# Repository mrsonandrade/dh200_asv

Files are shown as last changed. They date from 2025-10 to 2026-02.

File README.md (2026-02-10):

## DH200 ASV (Dragon Head 200 Autonomous Surface Vessel)

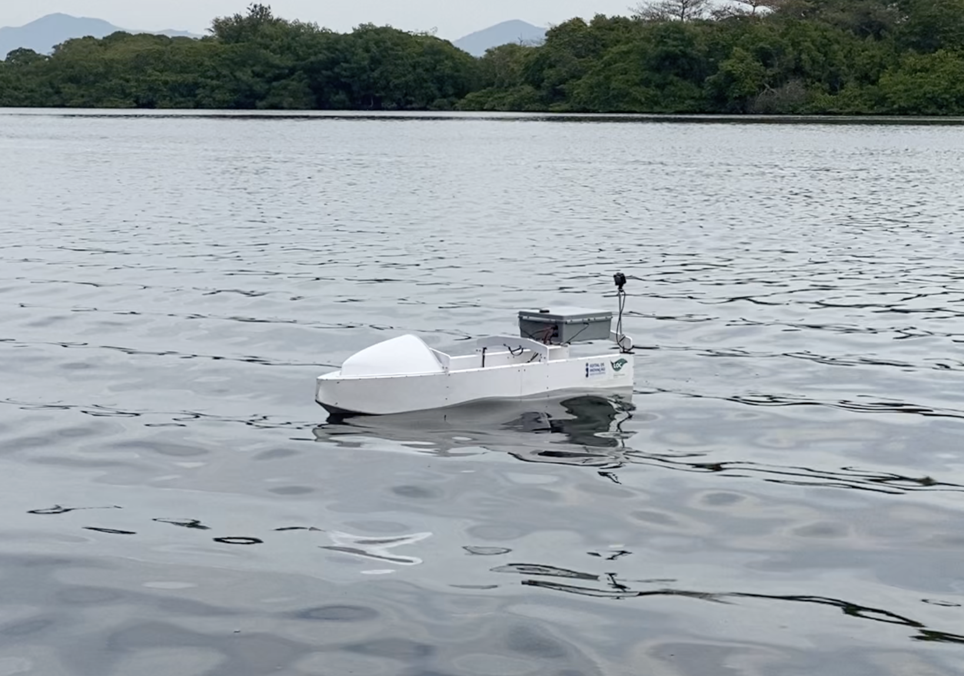
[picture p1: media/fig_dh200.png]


### .

Watch the video (https://www.youtube.com/watch?v=OJGZz4xJ2k4)

## Description

`dh200_asv` is a repository for the paper "A low cost, open-source, multipurpose autonomous surface vehicle".

The repository is structured by folders, each one with the following content:

- **`loc_mind`** – the “operating system” that runs inside the Raspberry Pi is here, as well as the graphical user interface (GUI) that runs in the land station. All the code is written in Python. Here, we call **LOC MIND** the _Modular Intelligent Navigation Device (MIND)_ created at the _Laboratório de Ondas e Correntes (LOC)_.
- **`rhino_files`** – a 3D CAD model for those who are familiar with the Rhinoceros software. This model contains the fully-opened hull configuration.
- **`fusion_files`** – a 3D CAD model for those who are familiar with the Fusion software. This model contains the fully-opened hull configuration with all details of screws, PVC sheets, electronic box, and so on.
- **`cnc_files`** – CNC (Computer Numerical Control) router files for those interested in replicating the hull of the ASV. The files (CRV3D format) are already prepared to be used in CNC machines.
- **`hydrostatics`** – this folder contains the hydrostatics table and the stability table, which are crucial for those planning to explore the capabilities of the ASV.
- **`hydrodynamics`** – as illustrated at the beginning of the paper, this folder contains tables of added mass and damping, load RAOs (Response Amplitude Operators), and displacement RAOs.
- **`docs`** – the main steps to replicate the ASV hull and electronics are in this folder, which contains PDF files and spreadsheets.
- **`media`** – this folder contains pictures and videos of the built ASV.

## Citing the Project

If you make use of the DH200 for your research, please cite our publication. Here is the corresponding BibTeX entry:

```
@article{Benatti2025,
  title = {A Low-Cost,  Open-Source,  Multi-Purpose Autonomous Surface Vehicle},
  volume = {13},
  ISSN = {2077-1312},
  url = {http://dx.doi.org/10.3390/jmse13122380},
  DOI = {10.3390/jmse13122380},
  number = {12},
  journal = {Journal of Marine Science and Engineering},
  publisher = {MDPI AG},
  author = {Benatti,  Thomaz Augusto Kras and de Andrade,  Emerson Martins and Correa,  Maicon Rodrigo and Lopes,  Felipe da Silva and Bernardino,  João Paulo Machado dos Santos and Sales,  Joel Sena and Fernandes,  Antonio Carlos},
  year = {2025},
  month = dec,
  pages = {2380}
}
```

## Contributing to the project
All kind of contributions are welcome: 
* Improvement of code with new features, bug fixes, and  bug reports
* Improvement of documentation
* Additional tests

If you have any ideas or questions, feel free to open an issue or contact us.

## Acknowledgements
The authors would like to thank the Programa de Recursos Humanos da Agência Nacional do Petróleo, Gás Natural e Biocombustíveis (PRH18-ANP) for their support, supported with resources from investment by oil companies qualified in the P, D\&I Clause of ANP Resolution no. 50/2015. This work was supported by the National Council for Scientific and Technological Development (CNPq), the Foundation for Research Support of the State of Rio de Janeiro (FAPERJ) through the ''Jovem Cientista do Nosso Estado'', the Instituto Reditus through the ''Edital de Inovação'', and [LOC/COPPE/UFRJ](https://www.loc.ufrj.br/index.php/en/) ([Laboratory of Waves and Current](https://www.loc.ufrj.br/index.php/en/) - [Federal University of Rio de Janeiro](https://ufrj.br/en/)).

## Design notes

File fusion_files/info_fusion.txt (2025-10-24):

Mass (only the electronics box):	3500 g
Dimensions electronics box (X,Y,Z): 375, 310, 140 mm
Centroide electronics box (X,Y,Z) : 255, 0, 405 mm
Mass (hull + electronics box):	32820 g

DATA (hull + electronics box):
Center of mass (same ref. as in Rhino):	756, -1, 156 mm
Moment of inertia w.r.t. the center of mass   (g mm^2):
	Ixx	1.459E+09
	Ixy	6.057E+06
	Ixz	1.792E+08
	Iyx	6.057E+06
	Iyy	1.060E+10
	Iyz	-2.794E+05
	Izx	1.792E+08
	Izy	-2.794E+05
	Izz	1.102E+10

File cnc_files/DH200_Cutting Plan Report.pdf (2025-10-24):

Cutting Plan Description

Issued by: Felipe da Silva Lopes Approved by: Joel Sena Sales Jr & Antonio Carlos Fernandes
ASV01 - CPR.A | Issued: 10/22/2025
PROJECT | Code: | ASV01
| Title: | DH-200 ASV – Cutting Plan Report
| Client: | Laboratory of Waves and Currents
| Effective date: | October 2025
| Manager: | Emerson Andrade
| Coordination: | Joel Sena Sales Jr & Antonio Carlos Fernandes

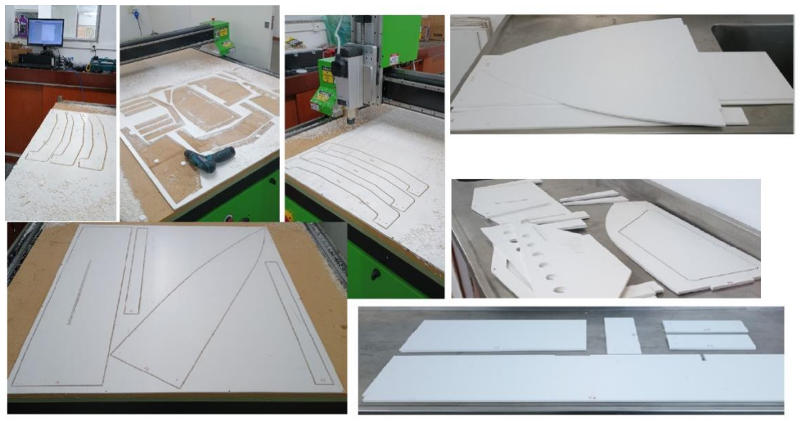
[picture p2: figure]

REPORT | Code: | CPR
| Title: | DH-200 – Cutting Plan Report
| Author: | Felipe da Silva Lopes
| Type: | Cutting Plan Description
| Revision: | A
| Issued: | 10/22/2025

Universidade Federal do Rio de Janeiro COPPE – Instituto Alberto Luiz Coimbra de Pós-Graduação e Pesquisa de Engenharia Laboratório de Ondas e Correntes (LOC)

ASV01 - CPR.A | 10/22/2025 | Page 2 of 10

### DOCUMENT HISTORY

Revision | Date | Issued by | Reviewed by | Approved by | Comments
A | 10/22/2025 | FSL | EA | EA | First version.
Revision | Date | Issued by

Reviewed
by

Approved
by | Comments

Notes:

FSL = Felipe da Silva Lopes

EA = Emerson Andrade

Laboratório de Ondas e Correntes (LOC)

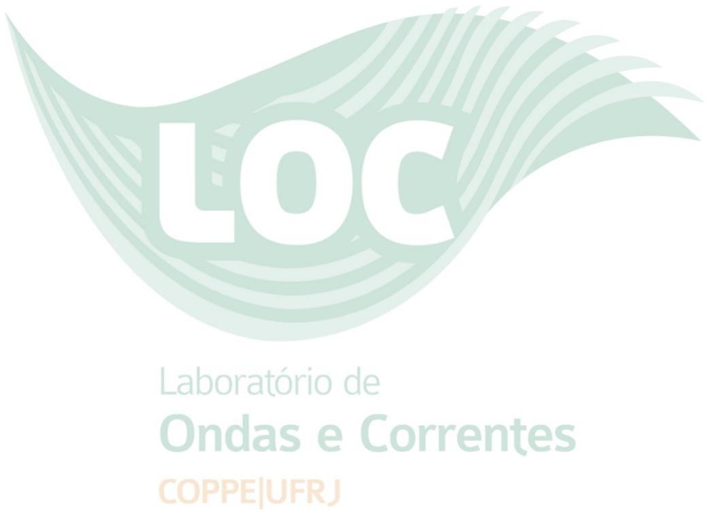
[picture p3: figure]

This document corresponds to an internal report referring to a procedure performed at the

Laboratory of Waves and Currents (LOC – COPPE/UFRJ) and all rights are reserved thereto. Any

partial of full reproduction of the contents in this report without proper authorization is

prohibited, under penalty of adopting appropriate measures in the civil and criminal spheres if

necessary.

Laboratório de Ondas e Correntes (LOC)

### TABLE OF CONTENTS

Laboratório de Ondas e Correntes (LOC)

### 1. Introduction

This document aims to provide step-by-step guidance on cutting parts for the Autonomous Surface Vessel (ASV) hull. The cutting process began with the receipt of the 3D file in Rhinoceros format (.3dm) with the parts properly identified. The parts were then flattened, their respective cut lines, holes, roughing, and other details to be machined were extracted, and the files were saved in .dxf format. Aspire-Vectric CAD/CAM software was used to program the machining tools for each cutting stage and plan the cutting sequence according to the assembly sequence. The CNC router was activated and configured for the origin (zero points), to receive the files saved in Mach 2/3 Arcs (mm) (*.txt) format, and loaded into the Mach 3 CNC software, where the commands and cutting coordinates for the parts were executed (see Figure 1).

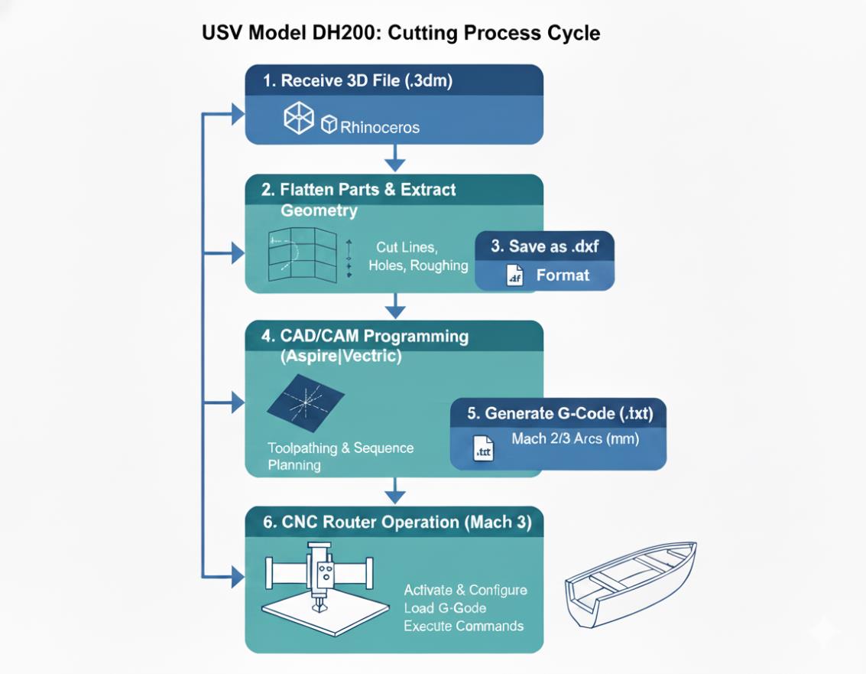
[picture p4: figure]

Figure 1 - Cutting Process Cycle.

Laboratório de Ondas e Correntes (LOC)

### 2. Plate development

In this process, Rhinoceros software was used to create a separated file for manipulating the hull plates. These parts were separated by thickness so they could be pre-arranged. The development was done using the unrollsurface command, which essentially consists of flattening each hull plate into 2D. At the end of this process, it was necessary to convert the file from meters to millimeters, as the CAD/CAM software uses this unit of measurement (Figure 2).

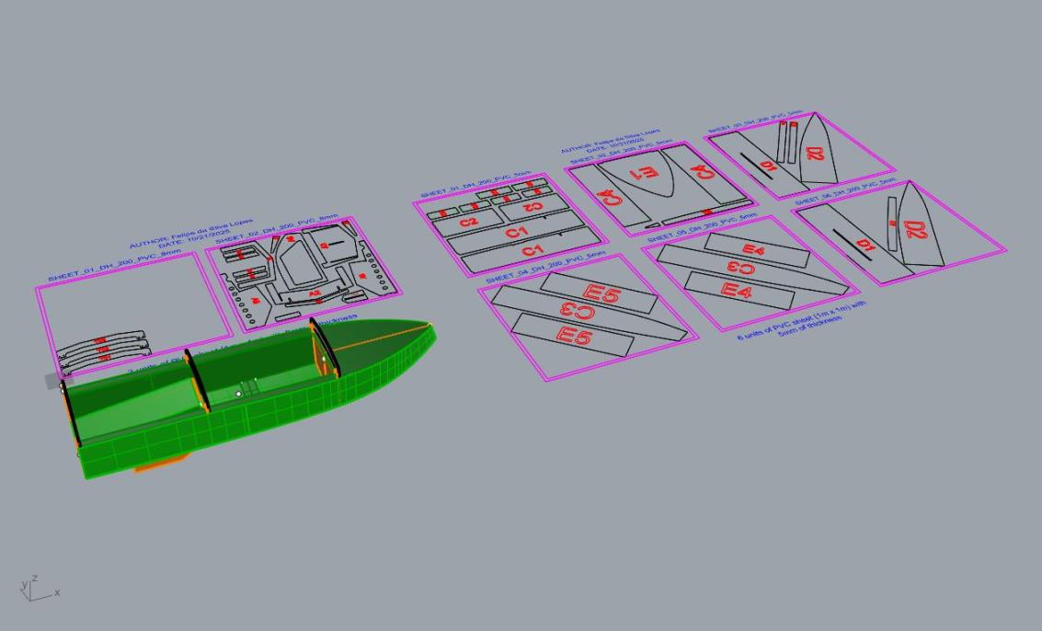
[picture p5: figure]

Figure 2 – Development of the DH_200.

### 3. Nesting

The 5mm and 8mm thick sheet layers were created with the cutting, text, and engraving needs. The 1000mm x 1000mm (1m x 1m) sheets were designed with a 20mm cutting margin for fixing the sheet in the CNC by using screws. The spacing between pieces of 12mm was also assumed. Thus, it was possible to organize and align, optimizing each piece on the sheets as much as possible, in order to avoid material waste. In this case, the 5mm and 8mm thick white PVC sheet material was used (Figure 3). The original files for this step were saved as: DH_200__CUT_PLAN_PVC_SHEET_5mm.dxf and DH_200__CUT_PLAN_PVC_SHEET_8mm.dxf.

Laboratório de Ondas e Correntes (LOC)

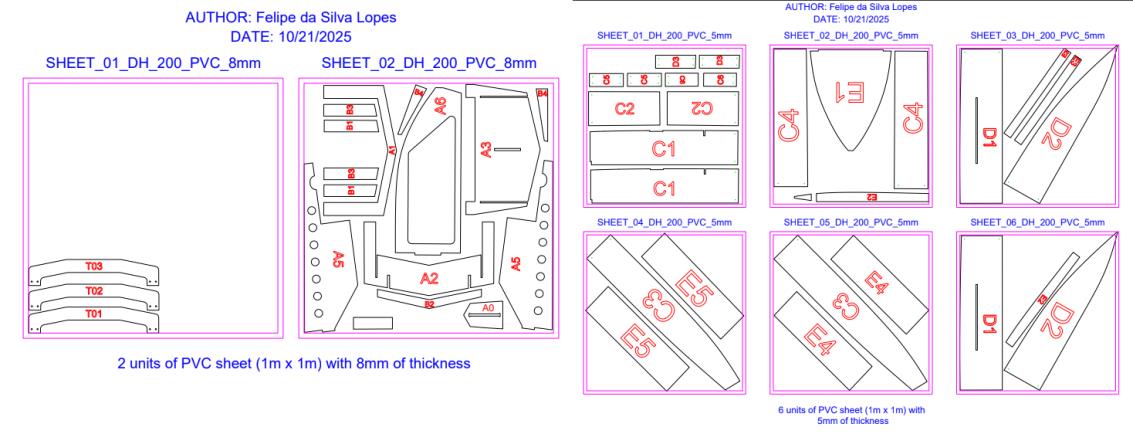
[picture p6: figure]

Figure 3 – Nesting parts organized by sheet.

### 4. CAD/CAM Programming

In this step, Aspire version 8 software was used, and the .dxf files previously prepared for cutting were loaded. Initially, a cutting area of 1000mm wide (x axis) x 1000mm high (y axis) was determined, with a thickness of 5mm or 8mm depending on the sheet (Figure 4 and 5). Then, the .dxf file was imported, and the cutting were marked in the toolpath tab, where the cutting settings were configured, such as: Cutting Depth, Machining Tool, Machining Direction, and Cutting Ramp. A single-flute milling cutter with a 4mm diameter and a 2mm cutting depth, spindle speed of 18.000 rpm, feed rate of 1.620 mm/s, and plunge rate of 810 mm/s was used.

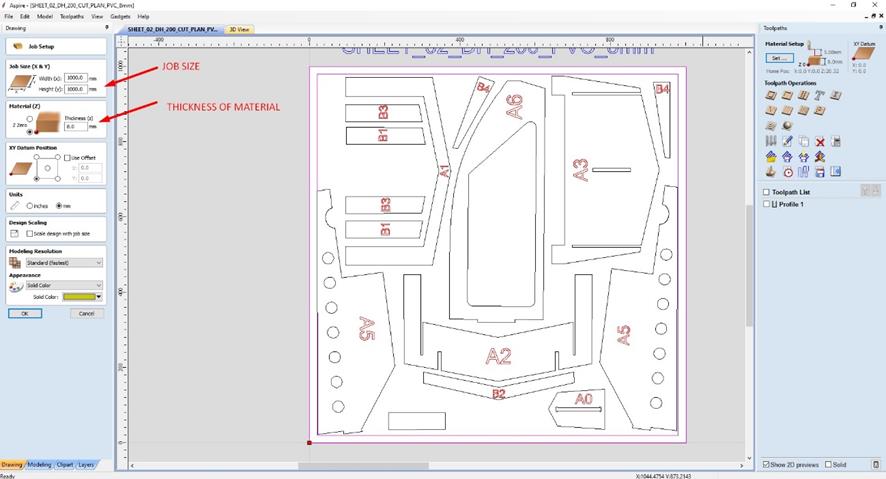
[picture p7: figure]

Figure 4 – Pre-set Job Setup.

Laboratório de Ondas e Correntes (LOC)

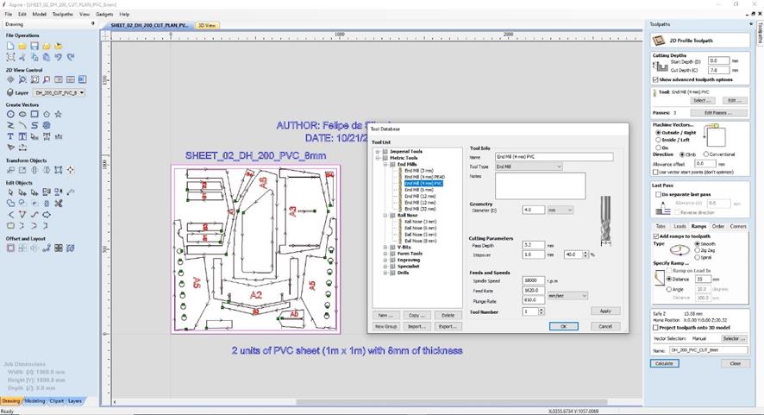
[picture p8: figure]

Figure 5 – 2D Profile Toolpath.

### 5. CNC Cutting Process

The CNC router used was a 3-axis (x, y, z) with a 1.2m x 2.5m cutting area (Figure 6), controlled by the Mach 3 software, which is widely used in this type of machine. It works using G-Code programming language, widely used in Computer Numerical Control (CNC) machines. Before operating the machine, Personal Protective Equipment (PPE) such as safety glasses, ear protection, and gloves must be worn. Extreme caution should be exercised when operating this machinery, as it can cause serious injury. Once these precautions are taken, the following steps should be taken:

- Fix the sheet metal to the table with screws
- Turn on the machine
- Recognize the machine's zeros
- Set the cutting zeros for the x and y axes at the corner of the sheet metal and the z axis at the cutting table
- Load the cutting files
- Start cutting

Laboratório de Ondas e Correntes (LOC)

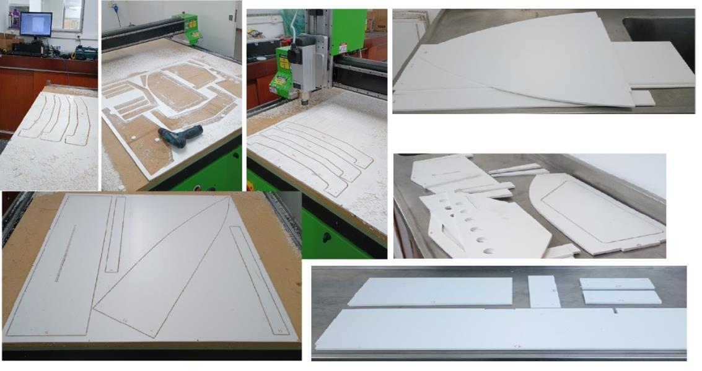
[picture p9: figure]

Figure 6 – CNC Cutting Process Overview.

Laboratório de Ondas e Correntes (LOC)

### 6. References

- | Robert | McNeel | & | Associates. | Rhinoceros | 8 | [software]. | Available | at:

https://www.rhino3d.com/. Accessed on: October 22, 2025.

- | VECTRIC | Ltd. | Aspire | [software]. | Available | at:

https://www.vectric.com/products/aspire/. Accessed on: October 22, 2025.

- | ARTSOFT | USA | / | MachSupport. | Mach3 | [software]. | Available | at:

https://www.machsupport.com/software/mach3/. Accessed on: October 22, 2025.

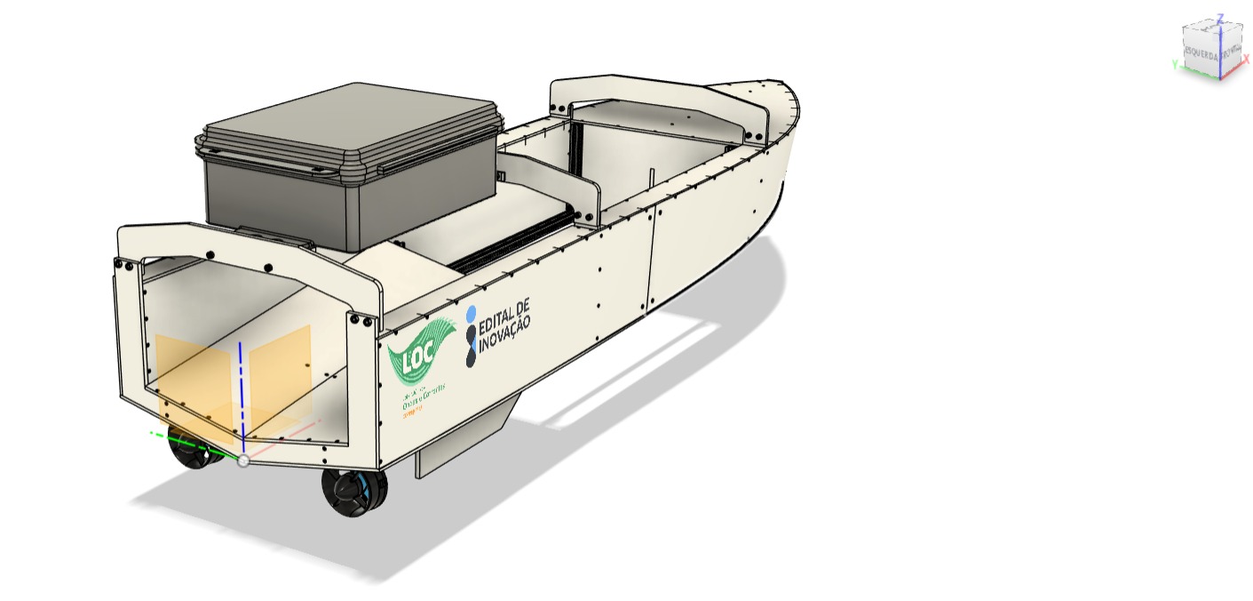
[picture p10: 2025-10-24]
fusion_files/images/fig_0.jpg

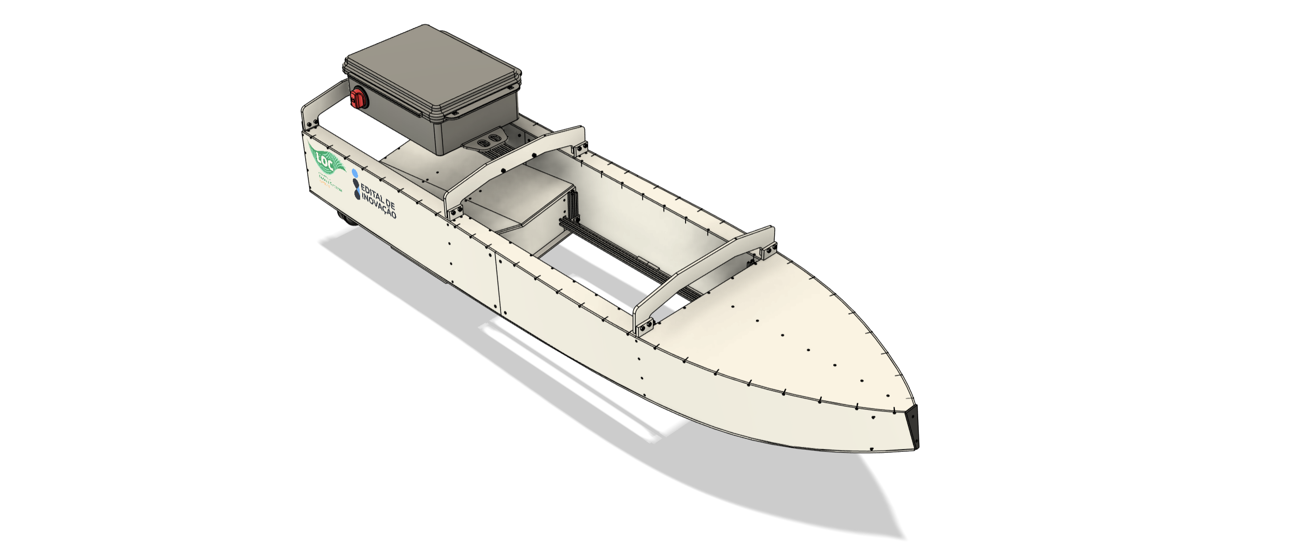
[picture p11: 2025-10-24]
fusion_files/images/fig_1.png

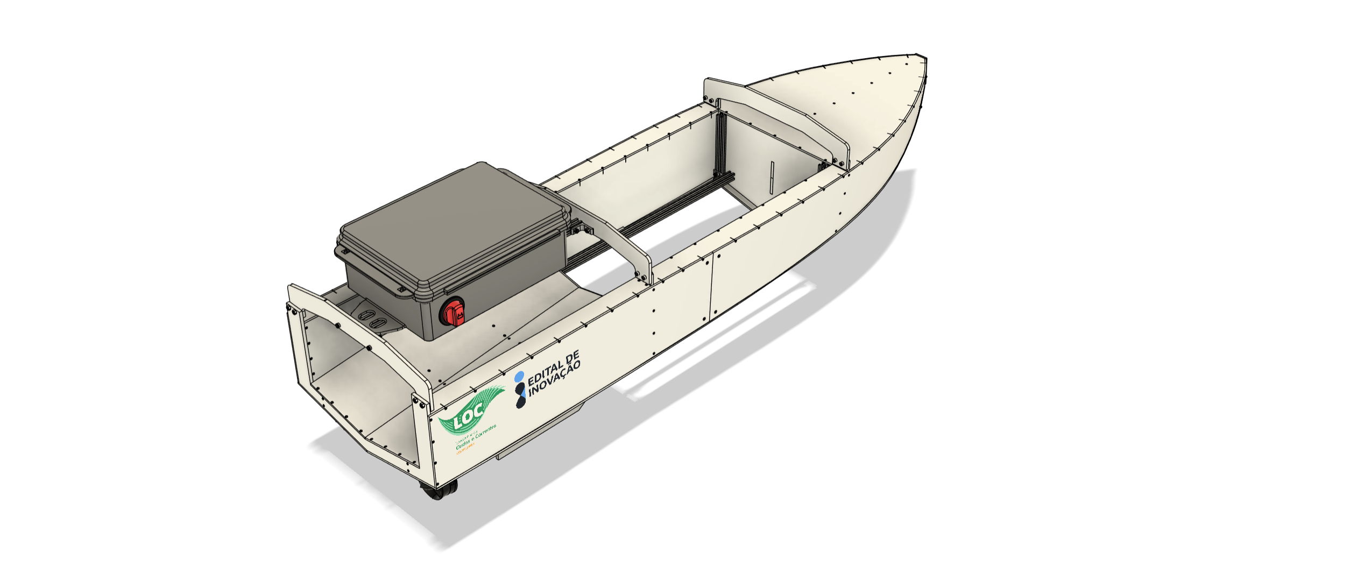
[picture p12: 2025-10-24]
fusion_files/images/fig_3.png

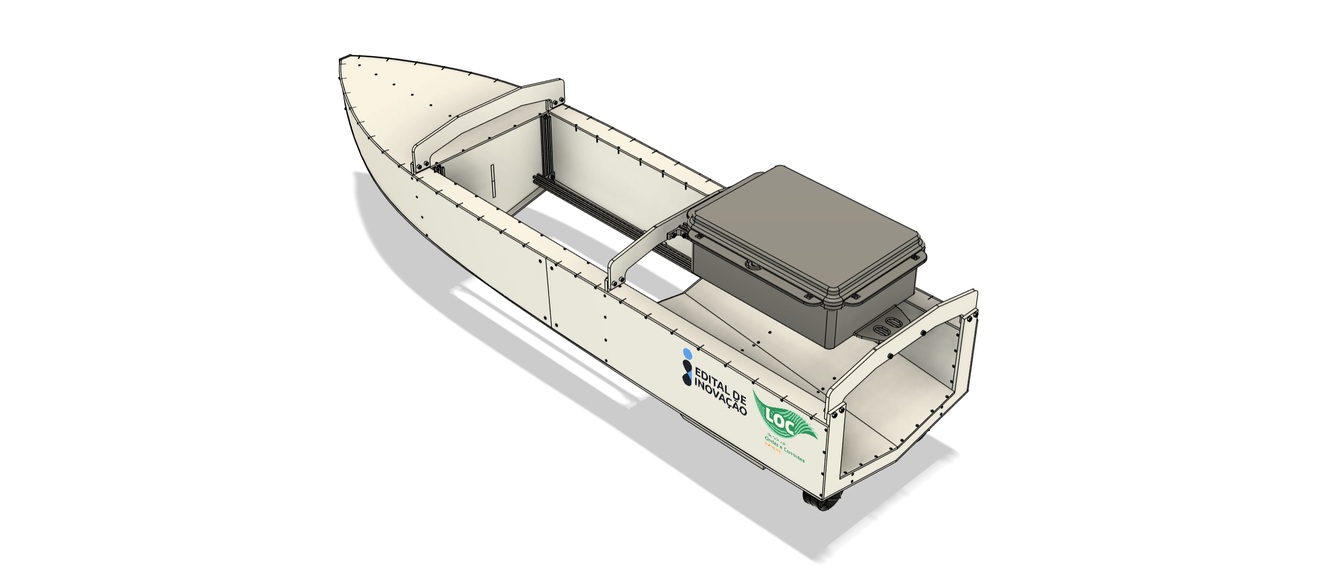
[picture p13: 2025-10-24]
fusion_files/images/fig_2.png

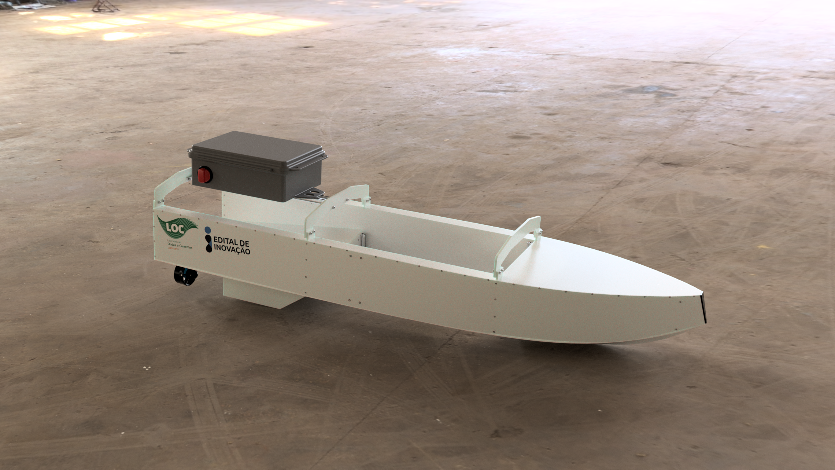
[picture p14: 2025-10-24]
fusion_files/images/fig_hangar_2.png

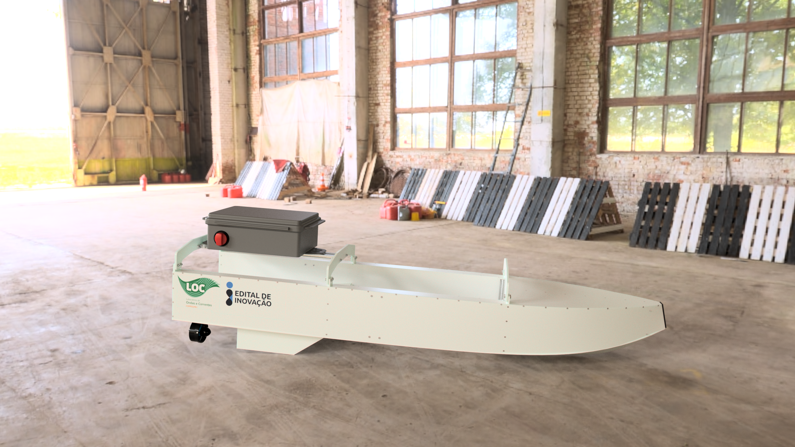
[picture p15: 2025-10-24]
fusion_files/images/fig_hangar_1.png

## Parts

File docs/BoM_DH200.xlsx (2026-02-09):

Description | Quantity | Brazil URL
Flat Allen Screw MA 3 x 20 Stainless Steel 304/A2 | 216 | https://www.parafusofacil.com.br/ProdutosDetalhes.php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
Flat Allen Screw MA 4 x 20 Stainless Steel 304/A2 | 12 | https://www.parafusofacil.com.br/ProdutosDetalhes.php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
Cylindrical Allen Screw MA 6 x 16 Stainless Steel 304/A2 | 28 | https://www.parafusofacil.com.br/ProdutosDetalhes.php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
Hex Nut MA 6 - 1.00 Wrench 10 Stainless Steel 304/A2 | 16 | https://www.parafusofacil.com.br/ProdutosDetalhes.php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
Rectangular Nut for Aluminum Profile M6 Base 20 | 12 | https://loja.alu-cek.com.br/porca-retangular-m6-base-20
Aluminum Bracket 38x38x15 mm for Profiles Base 15 and 20 | 8 | https://loja.forsetisolucoes.com.br/cantoneira-38x38x15mm-em-aluminio-p-perfis-base-15-20-v-t-slot-vslot-tslot-openbuilds
Structural Aluminum Profile 20x20 V-Slot - Channel 6 (1 meter) | 5 | https://www.mercadolivre.com.br/perfil-de-aluminio-estrutural-vslot-20x20-kit-2-pecas/up/MLBU1661967724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
Gray Waterproof Box Master 43,6x32,6x14 cm Multitoc | 1 | https://www.mercadolivre.com.br/caixa-hermetica-cinza-master-436x326x14cm-multiuso-multitoc/p/MLB23949260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
Rigid PVC Sheet White 1000 x 1000 x 5 mm | 6 | https://www.plastolandia.com.br/chapa-pvc-rigida-branca-2000-x-1000-x-5-mm
Rigid PVC Sheet White 1000 x 1000 x 8 mm | 2 | https://www.plastolandia.com.br/chapa-pvc-rigida-branca-2000-x-1000-x-5-mm
Bateria Lipo Ultra 5200mah 11.1v | 2 | https://www.mercadolivre.com.br/bateria-lipo-ultra-5200mah-111v-3s-50c-100c-xt60-arrma-hpi/p/MLB28739474
GPS GY-NEO6MV2 | 1 | https://www.robocore.net/sensor-robo/modulo-gps-gy-neo6mv2-com-antena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
XBEE PRO S1 | 2 | https://www.aliexpress.com/p/tesla-landing/index.html?scenario=c_ppc_item_bridge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
USB to Serial Adapter for XBEE | 2 | https://www.autocorerobotica.com.br/modulo-adaptador-usb-xbee-explorer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
Raspberry Pi 4 (8 GB) | 1 | https://www.robocore.net/placa-raspberry-pi/raspberry-pi-4-8gb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
Arduino Mega 2560 R3 | 1 | https://www.eletrogate.com/mega-2560-r3-cabo-usb-para-arduino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
Motor 2212 1400kv + ESC 40A | 2 | https://www.mercadolivre.com.br/kit-motor-2212-1400kv--esc-40a--helices-8040/up/MLBU777724503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
3D print PLA filament | 1 | https://esunbrasil.com.br/produto/esun-pla-white-1-75mm-1kg/
Electrical Wires (1 meter each) | 10 | https://produto.mercadolivre.com.br/MLB-3606613917-cabo-eletrico-estanhado-nautico-15mm-10-metros-conduferes-_JM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
Battery Switch | 1 | https://www.mercadolivre.com.br/chave-geral-p--2-baterias-nautico-profissional-4-posicoes/up/MLBU1977383377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
GPS Antenna WT1997 SMA – 5 meters | 1 | https://produto.mercadolivre.com.br/MLB-1324014329-antena-gps-wt1997-sma-5m-rastreadores-multimidia-_JM
SMA Antenna 3 dBi Wi-Fi 433 MHz | 1 | https://produto.mercadolivre.com.br/MLB-5800172920-cabo-pigtail-ufl-ipx-para-sma-antena-24ghz-3dbi-wi-fi-_JM
Compass | 1 | https://www.mercadolivre.com.br/modulo-bussola-eletronica-hmc5883l-gy-273/p/MLB2038778329
WiFi Router | 1 | https://www.amazon.com.br/Roteador-TP-Link-Roteadores-MW301R/dp/B07F24FXYY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
High-Strength PVC Adhesive 400 g | 2 | https://www.mercadolivre.com.br/cola-adesivo-para-cano-pvc-caixa-com-48-unidades/p/MLB39310385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

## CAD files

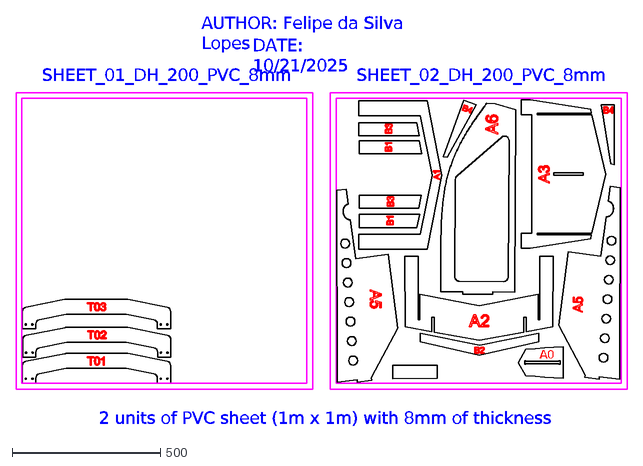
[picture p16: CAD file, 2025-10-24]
cnc_files/dxf_files/DH_200__CUT_PLAN_PVC_SHEET_8mm.dxf
2 units of PVC sheet (1m x 1m) with 8mm of thickness
AUTHOR: Felipe da Silva Lopes
DATE: 10/21/2025
A0
SHEET_01_DH_200_PVC_8mm
SHEET_02_DH_200_PVC_8mm

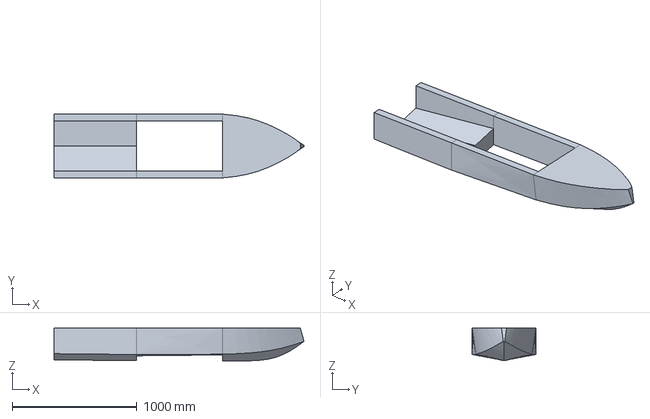
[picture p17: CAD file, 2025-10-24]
rhino_files/hull_asv.igs
2000.0 x 511.9 x 260.4 mm

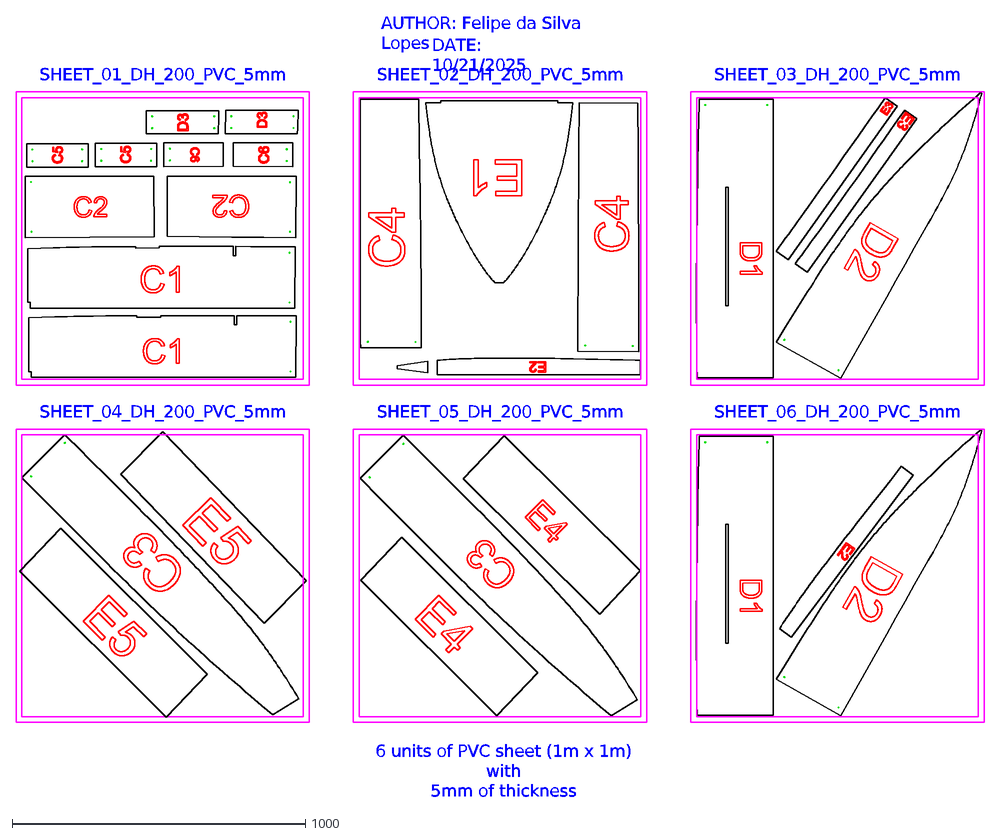
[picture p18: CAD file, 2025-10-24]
cnc_files/dxf_files/DH_200__CUT_PLAN_PVC_SHEET_5mm.dxf
AUTHOR: Felipe da Silva Lopes
DATE: 10/21/2025
6 units of PVC sheet (1m x 1m) with 5mm of thickness
SHEET_03_DH_200_PVC_5mm
SHEET_06_DH_200_PVC_5mm
SHEET_02_DH_200_PVC_5mm
SHEET_05_DH_200_PVC_5mm
SHEET_04_DH_200_PVC_5mm
SHEET_01_DH_200_PVC_5mm

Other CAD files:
rhino_files/hull_asv.3dm

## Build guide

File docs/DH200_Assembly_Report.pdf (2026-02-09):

Assembly Report

Issued by: Emerson & Thomaz Approved by: Joel Sena Sales Jr & Antonio Carlos Fernandes
ASV01 - ASR.A | Issued: 02/09/2026
PROJECT | Code: | ASV01
| Title: | DH-200 ASV
| Client: | Laboratory of Waves and Currents
| Effective date: | October 2025
| Manager: | Emerson Andrade
| Coordination: | Joel Sena Sales Jr & Antonio Carlos Fernandes

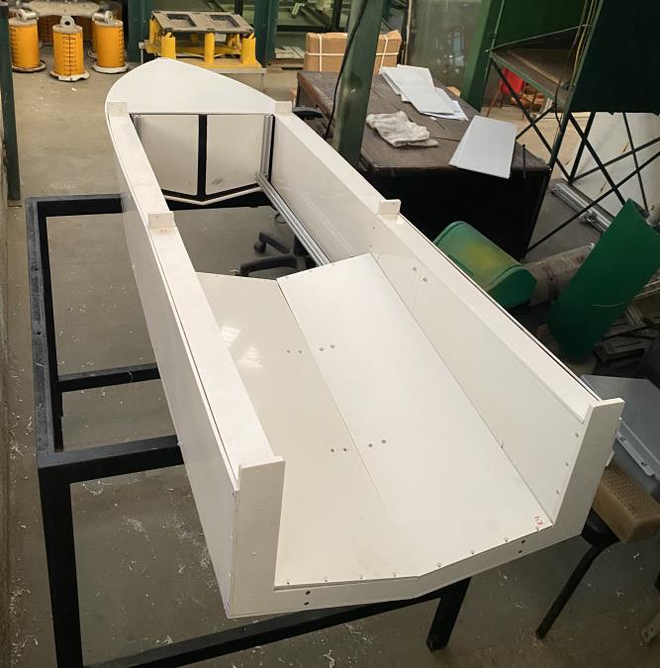
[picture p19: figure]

REPORT | Code: | ASR
| Title: | DH-200 – Assembly Report
| Author: | Emerson & Thomaz
| Type: | Assembly Report
| Revision: | A
| Issued: | 02/09/2026

Universidade Federal do Rio de Janeiro COPPE – Instituto Alberto Luiz Coimbra de Pós-Graduação e Pesquisa de Engenharia Laboratório de Ondas e Correntes (LOC)

ASV01 - ASR.A | 02/09/2026 | Page 2 of 13

### DOCUMENT HISTORY

Revision | Date | Issued by | Reviewed by | Approved by | Comments
A | 02/09/2025 | EA | EA | EA | First version.
Revision | Date | Issued by

Reviewed
by

Approved
by | Comments

Notes:

EA = Emerson Andrade

Laboratório de Ondas e Correntes (LOC)


This document corresponds to an internal report referring to a procedure performed at the

Laboratory of Waves and Currents (LOC – COPPE/UFRJ) and all rights are reserved thereto. Any

partial of full reproduction of the contents in this report without proper authorization is

prohibited, under penalty of adopting appropriate measures in the civil and criminal spheres if

necessary.

Laboratório de Ondas e Correntes (LOC)

### TABLE OF CONTENTS

Laboratório de Ondas e Correntes (LOC)

### 1. Introduction

This document aims to provide step-by-step guidance on assembling the hull plates of the Autonomous Surface Vessel (ASV) hull. Each plate has its identification defined in the “DH200_Cutting Plan Report.pdf” file, which can be checked into the files inside the “cnc_files” folder. Thus, Section 2 shows the illustration of the assembly, and Section 3 brings pictures of the real assembly. The plates were joined using screws and a standard PVC glue. For the screws, the holes and threads were done before joining. For the PVC glue, we used alcohol to clean the surface before applying the glue.

### 2. Main steps

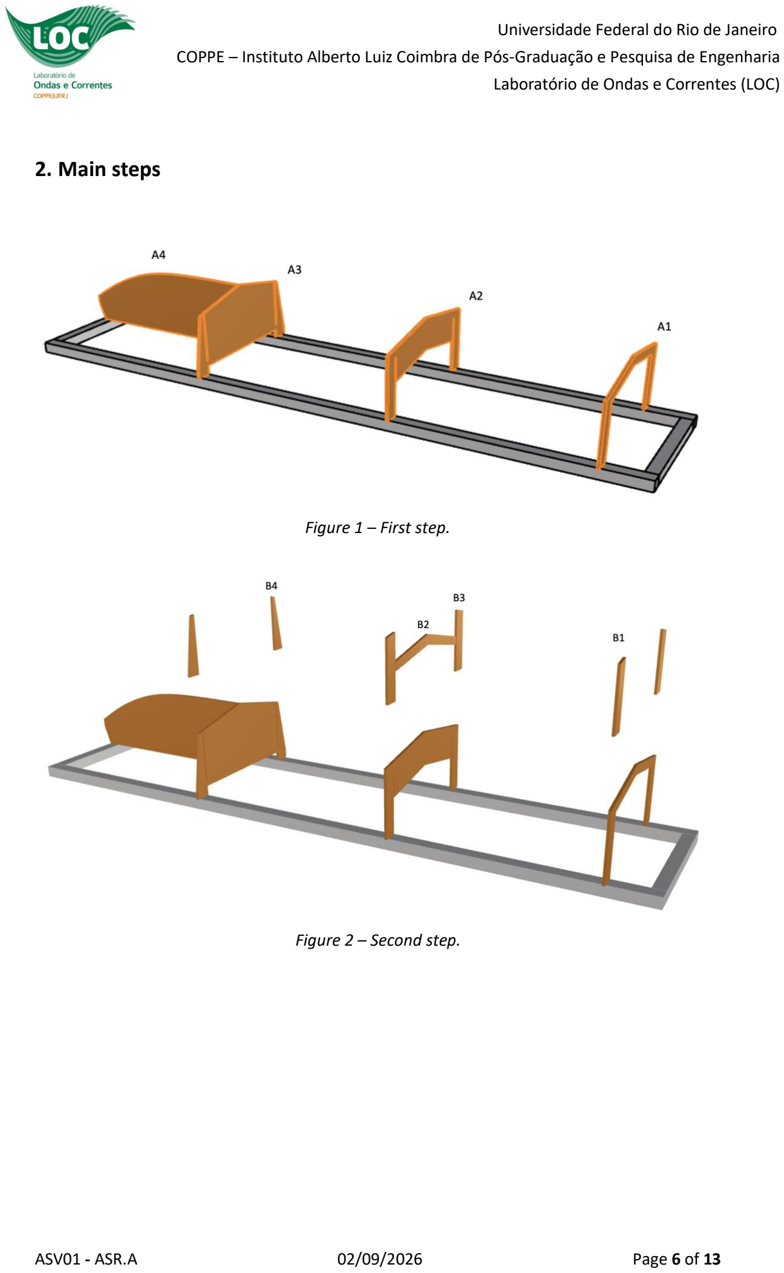
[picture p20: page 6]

Laboratório de Ondas e Correntes (LOC)

Figure 1 – First step.

Figure 2 – Second step.

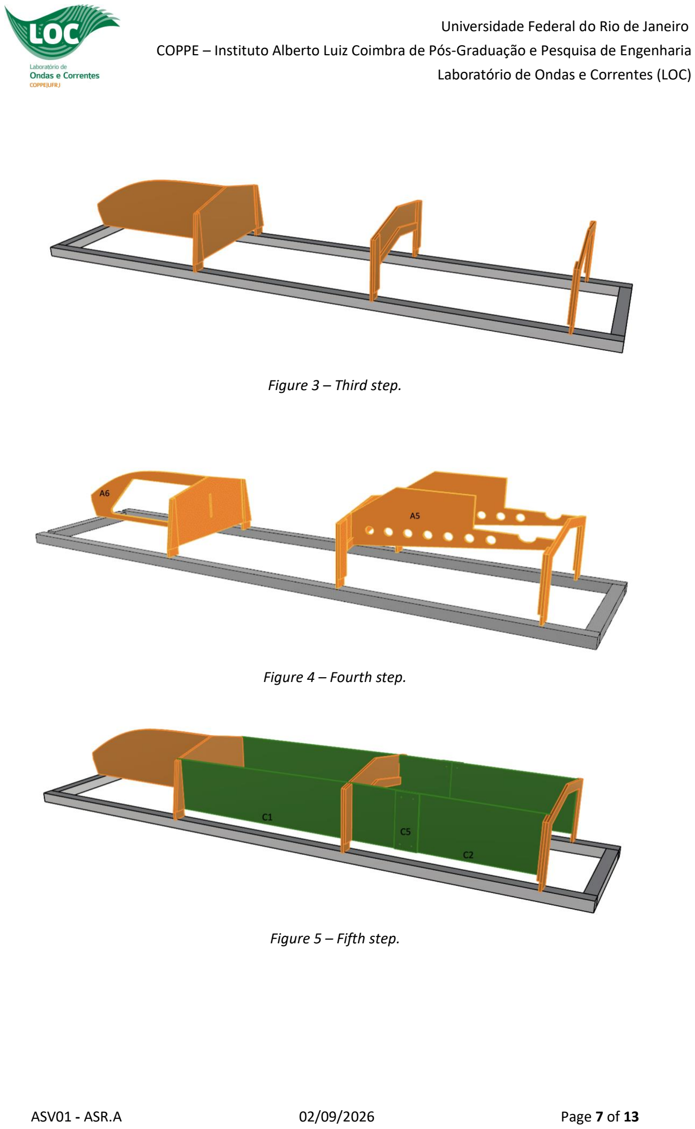
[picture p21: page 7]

Laboratório de Ondas e Correntes (LOC)

Figure 3 – Third step.

Figure 4 – Fourth step.

Figure 5 – Fifth step.

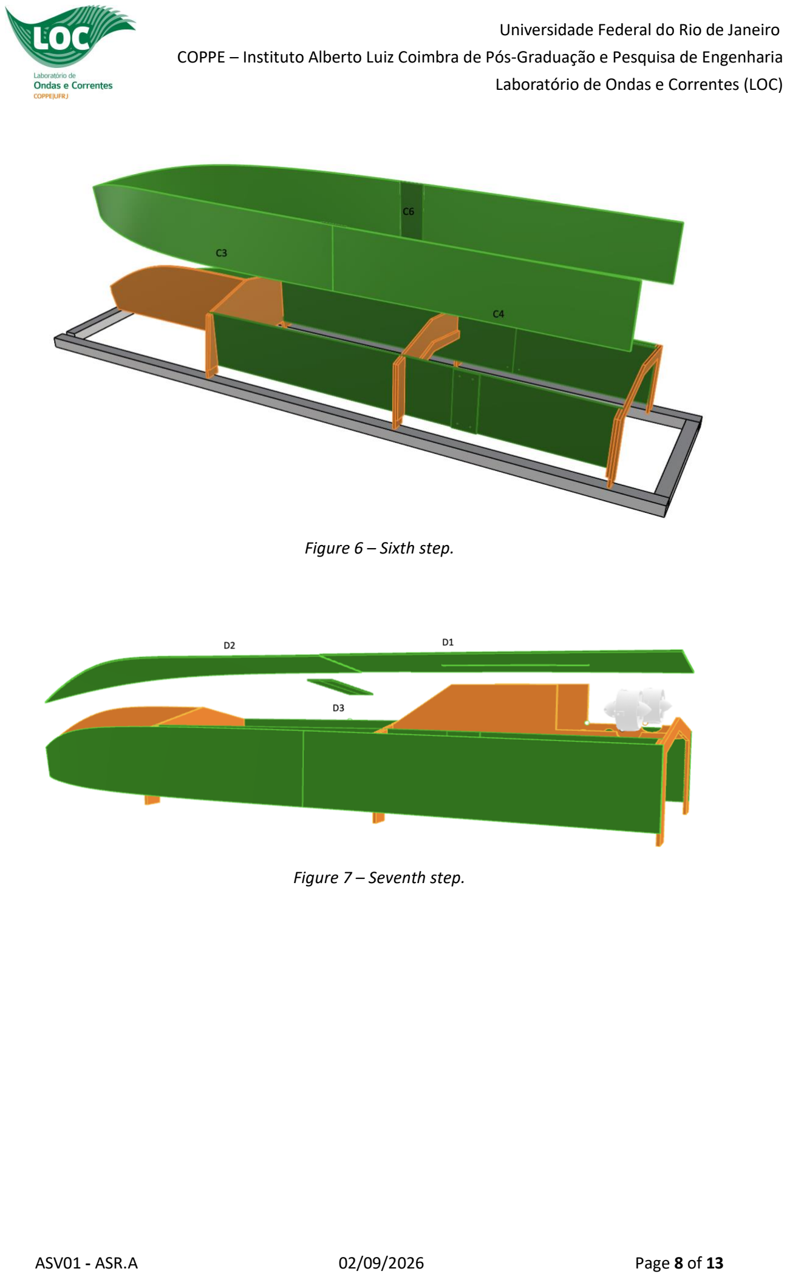
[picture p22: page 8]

Laboratório de Ondas e Correntes (LOC)

Figure 6 – Sixth step.

Figure 7 – Seventh step.

Laboratório de Ondas e Correntes (LOC)

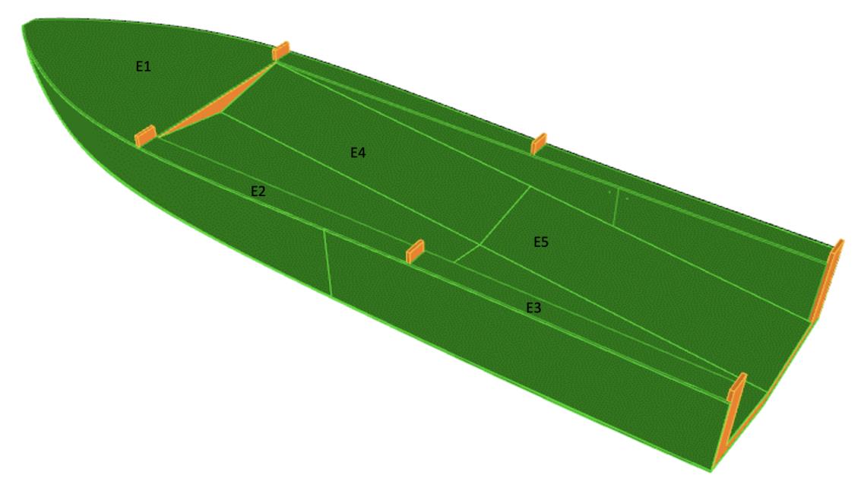
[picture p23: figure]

Figure 8 – Eighth step.

Laboratório de Ondas e Correntes (LOC)

### 3. Model assembly

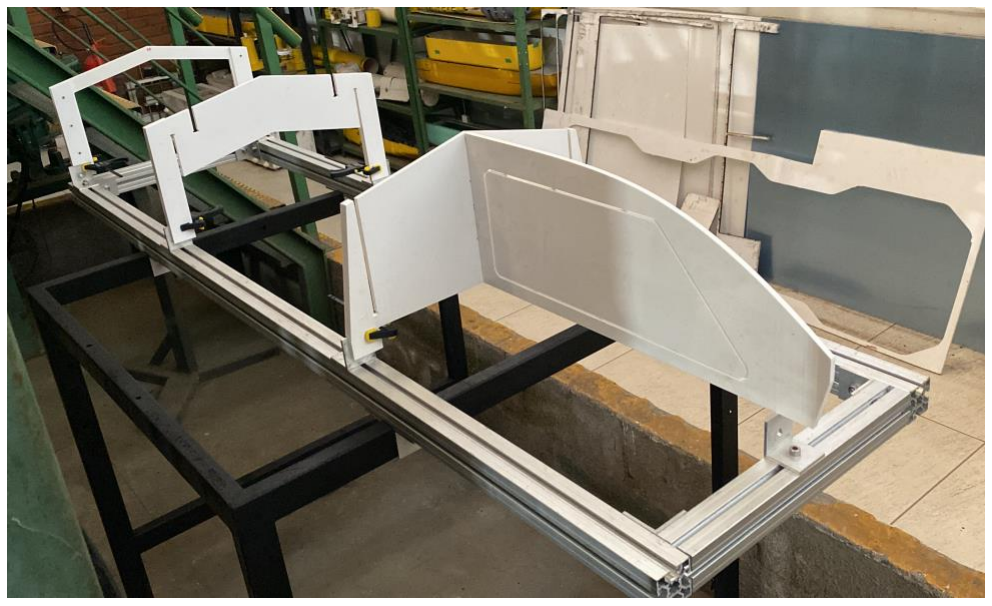
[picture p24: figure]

Figure 9 – Third step.

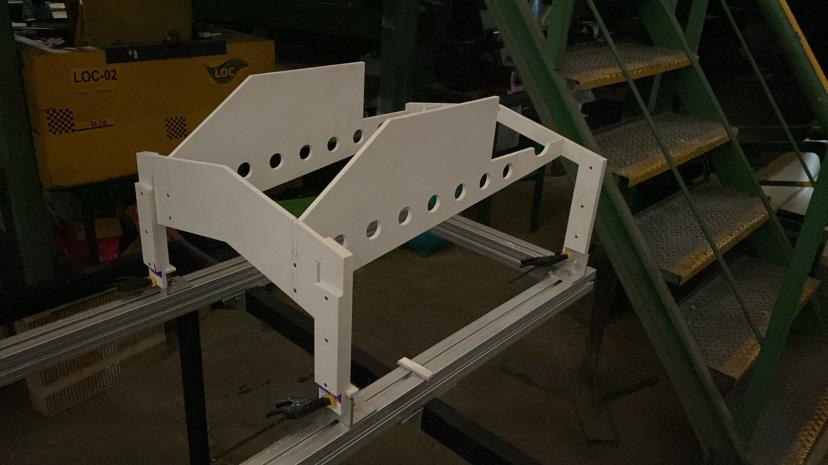
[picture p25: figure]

Figure 10 – Fourth step.

Laboratório de Ondas e Correntes (LOC)

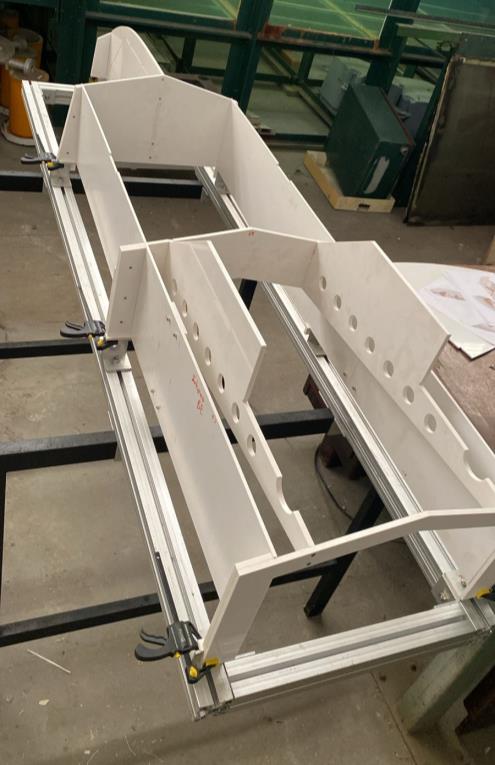
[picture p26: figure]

Figure 11 – Fifth step.

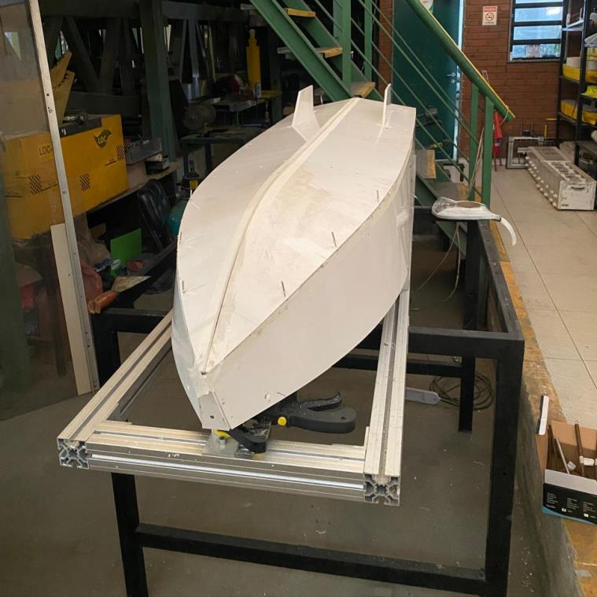
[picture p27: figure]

Figure 12 – Seventh step.

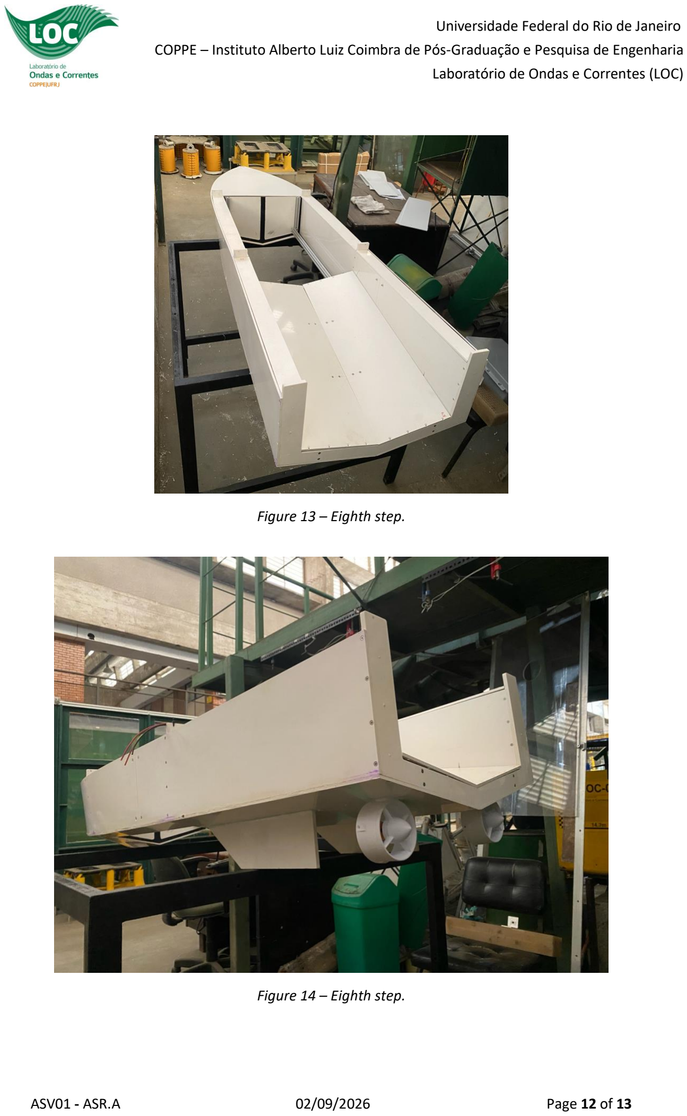
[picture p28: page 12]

Laboratório de Ondas e Correntes (LOC)

Figure 13 – Eighth step.

Figure 14 – Eighth step.

Laboratório de Ondas e Correntes (LOC)

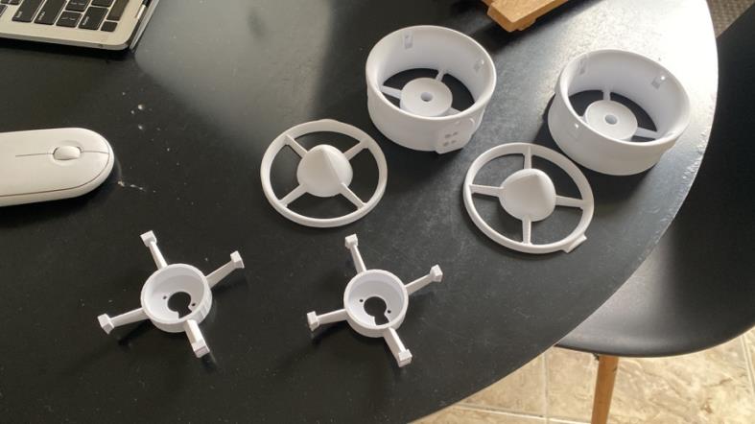
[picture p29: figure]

Figure 15 – 3D printed motors’ structure.

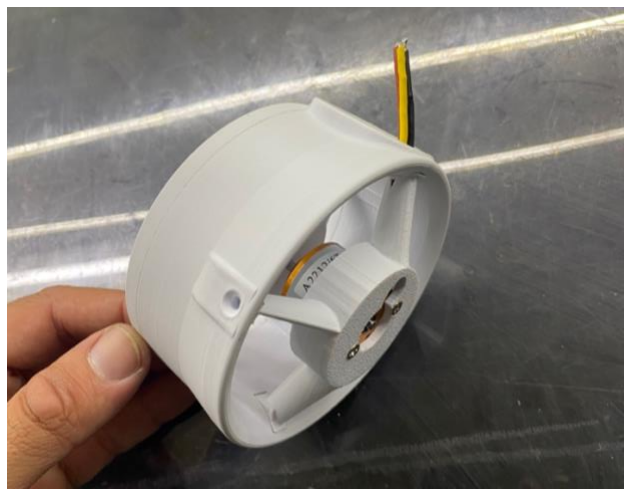
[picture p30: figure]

Figure 16 – 3D printed motors’ structure.

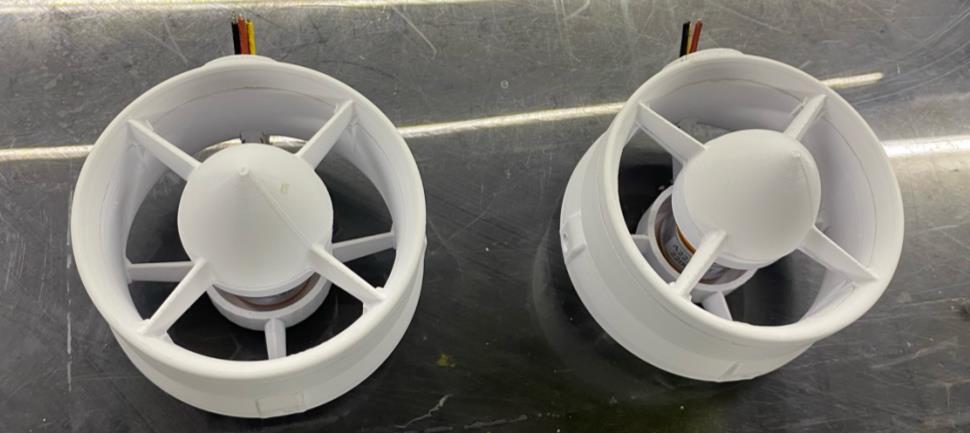
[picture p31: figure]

Figure 17 – 3D printed motors’ structure.

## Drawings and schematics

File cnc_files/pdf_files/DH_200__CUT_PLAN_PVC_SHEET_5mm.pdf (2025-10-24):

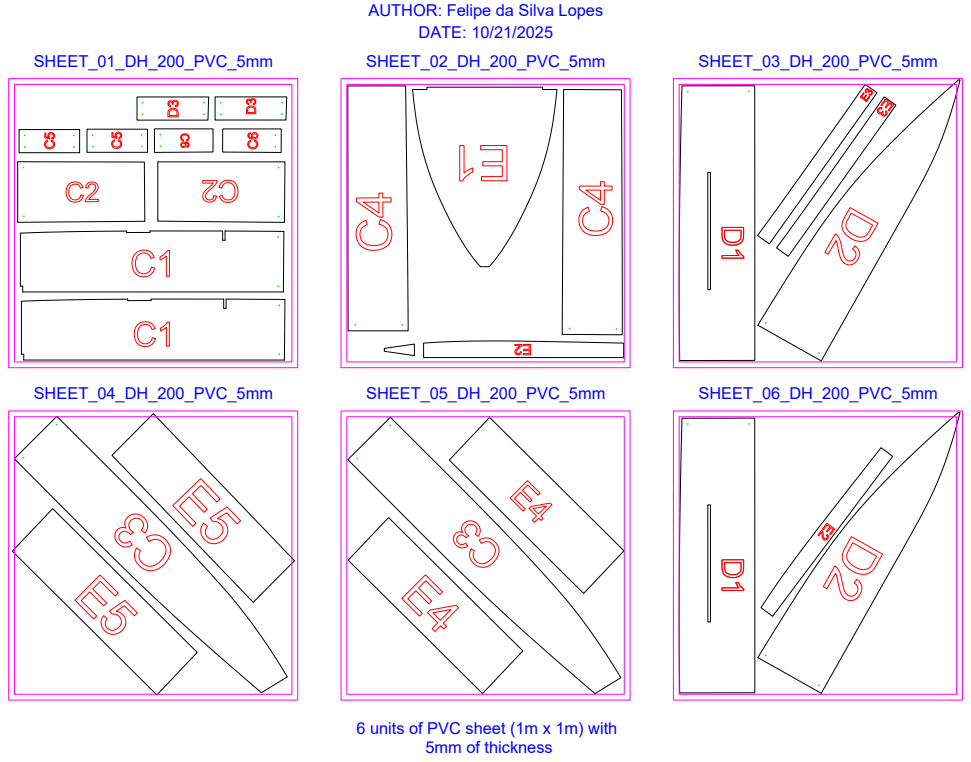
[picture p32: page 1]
DATE: 10/21/2025; SHEET_05_DH_200_PVC_5mm; SHEET_06_DH_200_PVC_5mm; SHEET_03_DH_200_PVC_5mm; 5mm of thickness; SHEET_01_DH_200_PVC_5mm; SHEET_04_DH_200_PVC_5mm; SHEET_02_DH_200_PVC_5mm

AUTHOR: Felipe da Silva Lopes

6 units of PVC sheet (1m x 1m) with

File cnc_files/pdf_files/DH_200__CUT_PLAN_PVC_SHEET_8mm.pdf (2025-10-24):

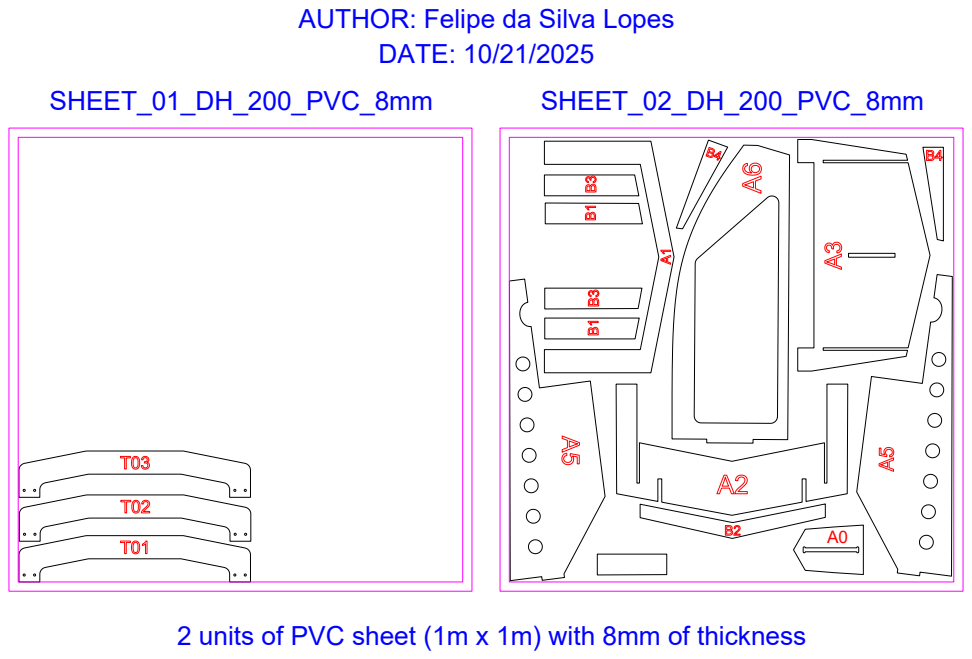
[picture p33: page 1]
SHEET_01_DH_200_PVC_8mm; DATE: 10/21/2025; SHEET_02_DH_200_PVC_8mm

AUTHOR: Felipe da Silva Lopes

2 units of PVC sheet (1m x 1m) with 8mm of thickness

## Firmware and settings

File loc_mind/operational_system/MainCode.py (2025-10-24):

#! /usr/bin/env python3

'''
@author: Emerson Martins de Andrade
COPPE/UFRJ     2025
Tested in Python 3.11.2
'''

# Did you start the pigpio daemon? E.g.
# sudo pigpiod

from DifferentialPropelledRobot import DifferentialPropelledRobot
from Robot import Robot # high-level robot logic
from XBee import XBee
from GPS import GPS
from Compass import Compass
from Sensors import GetAllSensors
from time import sleep

####################################################################
RobotID = '15' # CHANGE THIS ID FOR EACH ROBOT
####################################################################

Position = GPS()
Orientation = Compass()
Communication = XBee()
Motion = DifferentialPropelledRobot()
Sensors = GetAllSensors()

robot_kw = {'RobotID': RobotID,
            'Communication': Communication,
            'Motion': Motion,
            'Position': Position,
            'Orientation': Orientation,
            'Sensors': Sensors}

robot = Robot(**robot_kw) # high-level robot logic

threads = [Position, Orientation, Communication, Sensors, robot]
labels = ['Position','Orientation','Communication', 'Sensors', 'Robot']

print('Robot initialization complete!')

while True:

    for thread, label in zip(threads, labels):
        if not thread.main_loop.is_alive():
            msg = 'Restarted Main Thread in %s' % label
            thread._start_thread('main')
            print(msg)

    sleep(10)

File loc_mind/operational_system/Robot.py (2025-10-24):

#! /usr/bin/env python3

'''
@author: Emerson Martins de Andrade
COPPE/UFRJ     2025
'''

import ps.behaviors as pb
import ps.utils as pu
import numpy as np
import time
from threading import Thread
import math
from datetime import timezone 
import datetime


class Robot(Thread, object):

    def __init__(self, **kwargs):
        Thread.__init__(self)

        global Communication, Motion, Position, Orientation, Sensors
        self.robot_id = kwargs.pop('RobotID')
        Communication = kwargs.pop('Communication')
        Motion = kwargs.pop('Motion')
        Position = kwargs.pop('Position')
        Orientation = kwargs.pop('Orientation')
        Sensors = kwargs.pop('Sensors')

        self.reference_lat_lng = [-22.863593, -43.215014] # LabOceano Pier

        self.full_verbose = True
        self.save_log = True
        
        self.state_dict = {"robot_id": None, 
                        "x": None,
                        "y": None,
                        "yaw": None,
                        "time": None,
                        "lat": None,
                        "lng": None,
                        "time_gps": None,
                        "ph": None,
                        "conductivity": None,
                        "temperature": None}
                
        self.motors_on = 1
        self.motors_power = 0 # from 0 to 100%
        self.yaw_constant = 0.33
        self.waypoints_lat_lng = []
        self.waypoints = []
        self.radius_of_achieved_waypoint = 10.0 # meters
        self.angle_of_achieved_heading = 5.0 # degrees
        
        self.current_goal = 0

        # navigation modes
        self.start_waypoints = 0

        # swarm behavior settings
        self.swarm_centroid_as_position = 0
        
        self.activate_target = 1
        self.swarm_target = np.asarray([113.83, -334.25, 0.])
        self.swarm_target_lat_lng = [-22.866599, -43.213903]
        
        self.activate_repulsion = 0
        self.repulsion_alpha = 5.0
        self.repulsion_d = 2
        
        self.activate_aggregation = 0

        self.state_history = {
            'time': [],
            'time_gps': [],
            'x': [], # meters
            'y': [], # meters
            'reference_lat_lng': [],
            'lat': [],
            'lng': [],
            'yaw': [], # degrees
            'x_est': []
            }
        
        self.max_duty_cycle_motors = 100.0
        self.right_motor = 0
        self.left_motor = 0
        
        self.robots = {}
        self.neighbours = {}

        self.past_time_list = []

        self.timer_update = time.process_time() # starts the timer on
        self.timer_broadcast = time.process_time()
        self.timer_if_error = time.process_time()
        self.timer_log = time.process_time()

        self.heading_error_old = None
        self.heading_error_derivative = 0.0
    
        # Earth's radius in meters
        self.EARTH_RADIUS = 6378137.
        
        self.log_filename = datetime.datetime.now().strftime("log/log_%H%M%S_%d%m%Y.csv")
        self.f = open(self.log_filename, "a")
        self.f.close()

        self._start_thread('main')

    def _start_thread(self, name):
        if name == 'main':
            self.main_loop = Thread(target=self._update)
            self.main_loop.daemon = True
            self.main_loop.start()
            
    def log_state(self, state):
        self.f = open(self.log_filename, "a")
        self.f.write(str(state)+'\n')
        self.f.close()
    
    def check_poses(self, data):
        for key_id in data.keys():
            if key_id not in self.robots.keys():
                self.robots[key_id] = {}
            for key_info_type in data[key_id].keys():
                if key_info_type=="pose":
                    self.robots[key_id] = data[key_id][key_info_type]
                    
    def add_this_robot_to_data(self):
        if self.robot_id not in self.robots.keys():
            self.robots[self.robot_id] = {}

    def haversine_to_xy(self, lat1, lon1, lat2, lon2):
        # Convert latitude and longitude from degrees to radians
        lat1, lon1, lat2, lon2 = map(math.radians, [lat1, lon1, lat2, lon2])

        # Differences in coordinates
        dlat = lat2 - lat1
        dlon = lon2 - lon1

        # Haversine formula for distance
        a = math.sin(dlat / 2)**2 + math.cos(lat1) * math.cos(lat2) * math.sin(dlon / 2)**2
        c = 2 * math.atan2(math.sqrt(a), math.sqrt(1 - a))
        distance = self.EARTH_RADIUS * c  # Distance between points in meters

        # Calculate x and y coordinates in meters
        x = self.EARTH_RADIUS * dlon * math.cos((lat1 + lat2) / 2)
        y = self.EARTH_RADIUS * dlat

        return x, y
    
    def check_commands(self, data):
        
        try: self.motors_on = data[self.robot_id]['motors_on']
        except: pass
        try: self.motors_power = data[self.robot_id]['motors_power']
        except: pass
        
        try: self.waypoints_lat_lng = data[self.robot_id]['wpts_lat_lng']
        except: pass
        try: self.start_waypoints = data[self.robot_id]['start_waypoints']
        except: pass
        
        try: self.activate_target = data[self.robot_id]['activate_target']
        except: pass
        try: self.activate_repulsion = data[self.robot_id]['activate_repulsion']
        except: pass
        try: self.activate_aggregation = data[self.robot_id]['activate_aggregation']
        except: pass

        try: self.swarm_centroid_as_position = data[self.robot_id]['swarm_centroid_as_position']
        except: pass
        
        try: self.repulsion_alpha = data[self.robot_id]['repulsion_alpha']
        except: pass
        
        try: self.repulsion_d = data[self.robot_id]['repulsion_d']
        except: pass
        
        try: self.yaw_constant = data[self.robot_id]['yaw_constant']
        except: pass

    def adjust_heading(self, heading_error):
        
        if heading_error<-self.angle_of_achieved_heading: # turn right
            Motion.move(0.75*self.motors_power, -0.75*self.motors_power, 2)
            print('turnning right')

        elif heading_error>self.angle_of_achieved_heading: # turn left
            Motion.move(-0.75*self.motors_power, 0.75*self.motors_power, 2)
            print('turnning left')

        else:
            Motion.move(self.motors_power, self.motors_power)
            print('moving forward')

    def _update(self):

        while True:
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

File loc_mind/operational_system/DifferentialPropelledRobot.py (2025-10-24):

#! /usr/bin/env python3

'''
@author: Emerson Martins de Andrade
COPPE/UFRJ     2025
'''

import threading
import pigpio
import time
from time import sleep

class DifferentialPropelledRobot(object):

    def __init__(self):
      
        self.MOTOR_LEFT = 12
        self.MOTOR_RIGHT = 13
      
        self.pi = pigpio.pi()
        
        self.isbusy = False
        self._lock = threading.Lock()
        self._thread = None

    def calibrate(self):
        # calibrate ESC
        self.pi.set_servo_pulsewidth(self.MOTOR_LEFT, 2000)
        self.pi.set_servo_pulsewidth(self.MOTOR_RIGHT, 2000)
        time.sleep(2)
        self.pi.set_servo_pulsewidth(self.MOTOR_LEFT, 1000)
        self.pi.set_servo_pulsewidth(self.MOTOR_RIGHT, 1000)
        time.sleep(2)
        
    def move(self, leftDutyCycle, rightDutyCycle, delay=0):
        with self._lock:
            if self.isbusy:
                print('propulsion busy')
                return None
            self.isbusy = True
        
        self._thread = threading.Thread(target=self.move_in_thread, args=(leftDutyCycle, rightDutyCycle, delay,))
        self._thread.start()
        return self._thread

    def move_in_thread(self, leftDutyCycle, rightDutyCycle, delay=0):
        
        if leftDutyCycle<=0:
            left_pw = 1000
        elif leftDutyCycle>0:
            left_pw = int(1000 + 10*leftDutyCycle)
            
        if rightDutyCycle<=0:
            right_pw = 1000
        elif rightDutyCycle>0:
            right_pw = int(1000 + 10*rightDutyCycle)

        self.pi.set_servo_pulsewidth(self.MOTOR_LEFT, left_pw)
        self.pi.set_servo_pulsewidth(self.MOTOR_RIGHT, right_pw)
        
        sleep(delay)
        if delay==0:
          pass
        else:
          self.stop()
            
        with self._lock:
            self.isbusy = False
    
    def stop(self):
        self.pi.set_servo_pulsewidth(self.MOTOR_LEFT, 1000)
        self.pi.set_servo_pulsewidth(self.MOTOR_RIGHT, 1000)

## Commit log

2025-10-24 upload of files
    [DH_200__CUT_PLAN_PVC_SHEET_5mm.dxf, DH_200__CUT_PLAN_PVC_SHEET_8mm.dxf, hull_asv.3dm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]
2026-02-09 BoM and assembly docs
    [BoM_DH200.xlsx]
